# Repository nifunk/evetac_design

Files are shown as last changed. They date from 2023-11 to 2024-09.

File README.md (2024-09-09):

# evetac_design

<!-- PROJECT LOGO -->
<br />
<div align="center">
  <a href="https://github.com/nifunk/evetac_design">
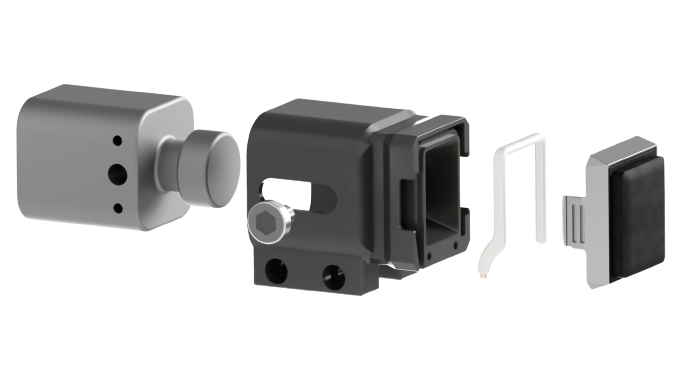
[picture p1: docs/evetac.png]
evetac_design
    
  </a>

  <h3 align="center">Evetac: An Event-based Optical Tactile Sensor
for Robotic Manipulation</h3>
  <h5 align="center">Niklas Funk, Erik Helmut, Georgia Chalvatzaki, Roberto Calandra, Jan Peters</h5>

  <p align="center">
    We introduce a new event-based optical tactile sensor called Evetac. Its modular design attempts to maximize the re-use of existing components to facilitate reproducibility. You can simply 3D print the housing and assemble the sensor yourself. This repo contains the mechanical design files of the sensor and additional adapters. They are designed to be 3D printed so that you are able to produce them yourself and/or modify them to fit your needs. <br />
    <a href="https://sites.google.com/view/evetac"><strong>For more information about Evetac, visit the Project Page. »</strong></a> <br />
    <a href="https://youtu.be/24e9n3mCopw"><strong>Click here for a Video Tutorial on how to assemble Evetac. »</strong></a>
  </p>
</div>

<!-- TABLE OF CONTENTS -->
<details>
  <summary>Table of Contents</summary>
  <ol>
    <li>
      <a href="#sensor-overview">Sensor Overview</a>
    </li>
    <li>
      <a href="#alternative-evetac-versions">Alternative Evetac Versions</a>
    </li>
    <li>
      <a href="#customization-and-3d-printing">Customization and 3D Printing</a>
    </li>
    <li>
      <a href="#questions-and-contributing">Questions and Contributing</a>
    </li>
    <li>
      <a href="#citing">Citing</a>
    </li>
  </ol>
</details>

<!-- Sensor Overview -->
## Sensor Overview
The sensor mainly consists of off-the-shelf components, as well as a 3D printed case for facilitating manufacturing and reducing the entry barrier into the field of event-based tactile sensing. You can find a detailed overview of the sensors components in the following table:

| Component | Specifications | References |
|---|---|---|
| Camera | DVXplorer Mini from Inivation, 640 x 480px resolution | <a href="https://shop.inivation.com">Inivation</a>  |
| Housing | Custom Design, 3D printed | <a href="/evetac_housing/evetac-housing.stl">Design File</a> |
| Camera Screws | 1/4", thread length 6.3mm | <a href="https://www.amazon.de/gp/product/B01AZ558WE/ref=ppx_yo_dt_b_asin_title_o01_s00?ie=UTF8&psc=1">Amazon</a> |
| LED stripe | LED COB band 4000K,  height 5mm, witdth 2.2mm, 12V  | <a href="https://www.amazon.de/gp/product/B09WHY4Q33/ref=ppx_yo_dt_b_asin_title_o00_s00?ie=UTF8&th=1">Amazon</a> |
| Gel | GelSight Mini Marker Gel | <a href="https://www.gelsight.com/product/tracking-marker-replacement-gel/">GelSight</a> |

All the adaptors for the Franka Emika Panda robot arm, Robotis RH-P12-RN gripper, and OptiTrack accessories that were used in the experiments can be found in the respective folders: <a href="/adapters">adapters</a> and <a href="/optitrack">optitrack</a>.

<!-- Alternative Evetac Versions -->
## Alternative Evetac Versions
To improve sensor reproducibility, we aim to provide additional Evetac Designs <a href="/evetac_housing/alternative_designs/">here</a>.
* December 2023: Adding support for the newly released DVXplorer Micro event-based camera from Inivation. 

<!-- Customization and 3D Printing -->
## Customization and 3D Printing
In case you want to customize the provided 3D models and print them on a 3D printer, you will need to download the .STEP files, modify them according to your needs and prepare it for the printer using specialized software. Here are the general steps to follow:

1. Choose a 3D modeling software: There are many 3D modeling software options available, both free and paid. Some popular options are <a href="https://www.autodesk.de/products/fusion-360">Fusion 360</a> or <a href="https://www.freecad.org/index.php?lang=de">FreeCAD</a>.
2. Customize the 3D model: Using the 3D modeling software, open the .STEP file of the object you want to edit and modify it to fit your needs. You can of course also create a new 3D model from scratch.
3. Export the file: Once the 3D model is complete, you will need to export it in a format that can be read by a 3D printer. The most common file format for 3D printing is .STL (STereoLithography).
4. Slice the file: The .STL file needs to be "sliced" into thin layers that the 3D printer can print one at a time. This is done using slicing software (e.g. <a href="https://ultimaker.com/de/software/ultimaker-cura">Cura</a> for <a href="https://de.wikipedia.org/wiki/Fused_Deposition_Modeling">FDM</a> 3D printers like the Prusa MK series), which takes the 3D model and creates a set of instructions that the 3D printer can understand.
5. Transfer the file: Once the file is sliced, it can be transferred to the 3D printer either through a SD Card, USB cable or wirelessly, depending on the printer.
6. Start printing: Load the 3D printer with the material you want to use (such as PLA or ABS), and start the printing process. The printer will then print the object layer by layer until it is complete.

Keep in mind that the specific steps for creating a 3D file may vary depending on the software and printer you are using. It is important to refer to the manufacturer's instructions and guides to ensure you are creating a file that is compatible with your 3D printer.

<!-- Questions and Contributing -->
## Questions and Contributing
If you have any questions or need help with setting up the sensor, please create an <a href="https://github.com/nifunk/evetac_design/issues/new">issue</a>.

We also welcome contributions to this repository, including new 3D models or other improvements. If you would like to contribute, please <a href="https://github.com/nifunk/evetac_design/fork">fork</a> this repository and submit a <a href="https://github.com/nifunk/evetac_design/compare">pull request</a> with your changes, or reach out to niklas [at] robot-learning [dot] de.

<!-- Citing -->
## Citing
If you use this project in your research, please cite it.

```
@ARTICLE{EvetacFunk,
  author={Funk, Niklas and Helmut, Erik and Chalvatzaki, Georgia and Calandra, Roberto and Peters, Jan},
  journal={IEEE Transactions on Robotics}, 
  title={Evetac: An Event-based Optical Tactile Sensor for Robotic Manipulation}, 
  year={2024},
  volume={},
  number={},
  pages={1-20},
  keywords={Robots;Tactile sensors;Optical sensors;Cameras;Robot vision systems;Optical feedback;Spatial resolution;Force and Tactile Sensing;Perception for Grasping and Manipulation;Deep Learning in Robotics and Automation;Event-based Sensing},
  doi={10.1109/TRO.2024.3428430}}
```

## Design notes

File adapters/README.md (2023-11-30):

# List of Adapters provided in this folder:

* <a href="/adapters/franka-robotis-interface.stl">franka-robotis-interface</a> - Interface part for attaching the Robotis Gripper to the end effector flange of the Franka Panda.
* <a href="/adapters/robotis-gripper-evetac-mount.stl">robotis-gripper-evetac-mount</a> - Part for attaching Evetac's mounting mechanism as a finger to the Robotis gripper. I.e., this part allows attaching Evetac's housing to the Robotis gripper.
* <a href="/adapters/gelsight-mini-evetac-mount.stl">gelsight-mini-evetac-mount</a> - Adapter for GelSight Mini such that it is compatible with Evetac's mounting mechanism.
* <a href="/adapters/robotis-gripper-gelsight-mini.stl">robotis-gripper-gelsight-mini</a> - Part for attaching GelSight Mini's mounting mechanism as a finger to the Robotis gripper. I.e., this part allows attaching GelSight Mini directly to the Robotis gripper.
* <a href="/adapters/franka-evetac-finger.stl">franka-evetac-finger</a> - Part for attaching Evetac as a single finger to the franka end effector mounting flange.
* <a href="/adapters/franka-gelsight-mini-finger.stl">franka-gelsight-mini-finger</a> - Part for attaching GelSight Mini as a single finger to the franka end effector mounting flange.
* <a href="/adapters/robotis-evetac-finger.stl">robotis-evetac-finger</a> - Part for attaching Evetac as a single finger to the franka-robotis-interface. Please note, this additionally requires inserting 4 threads into the holes on top using a soldering iron, such that the adapter can be connected to the robotis interface using screws.
* <a href="/adapters/robotis-gelsight-mini-finger.stl">robotis-gelsight-mini-finger</a> - Part for attaching GelSight Mini as a single finger to the franka-robotis-interface. Please note, this additionally requires inserting 4 threads into the holes on top using a soldering iron, such that the adapter can be connected to the robotis interface using screws.

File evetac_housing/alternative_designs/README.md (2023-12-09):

This folder provides additional Evetac Designs to improve reproducibility and recreate Evetac using different hardware components.

The table below lists the alternative sensor designs and which components deviate from the original design.

| Details | evetac_dvxplorer_micro  |
|---|---|
| Camera | DVXplorer Micro from Inivation, 640 x 480px resolution (from <a href="https://shop.inivation.com">Inivation</a>)  |
| Housing | Custom Design, 3D printed (<a href="/evetac_housing/alternative_designs/evetac_dvxplorer_micro/evetac_dvxplorer_micro-housing.stl">here</a>) |
| Camera Screws | 4 M2 Screws |
| LED stripe | Same as original Evetac |
| Gel | Same as original Evetac |

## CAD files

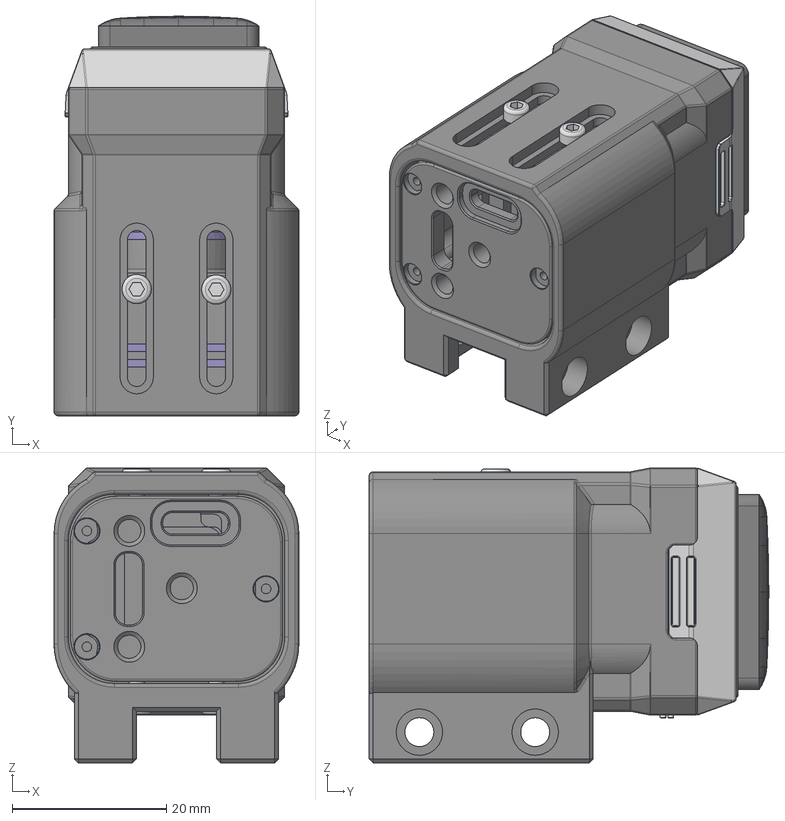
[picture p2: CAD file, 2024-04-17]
evetac_housing/alternative_designs/evetac_dvxplorer_micro/evetac_dvxplorer_micro-assembly.step
31.7 x 51.7 x 38.2 mm
evetac-housing
DVXplorer Micro 07.2023 Case v2
DVXplorer Micro 07.2023 Cover v2
evetac-gelsight-snapfitholder
Komponente2
Komponente3
Komponente2_1
screw x 4

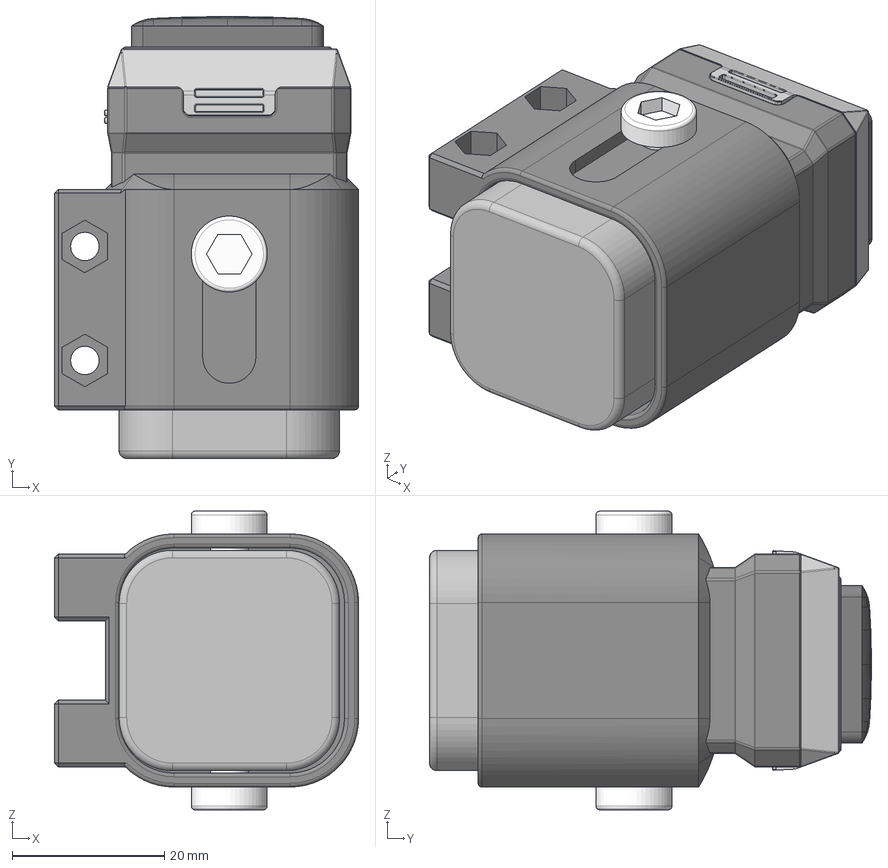
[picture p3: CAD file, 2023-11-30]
evetac_housing/evetac-assembly.step
40.0 x 58.1 x 39.3 mm
evetac-center
Komponente11
evetac-gelsight-snapfitholder
Komponente14
Komponente15
Komponente17
screw 1
screw 2

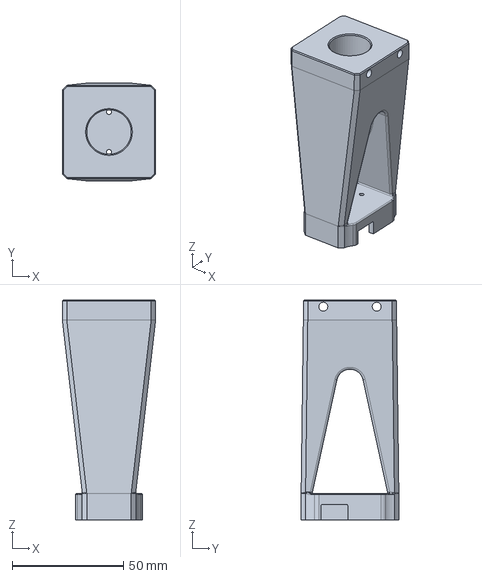
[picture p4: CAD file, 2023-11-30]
adapters/robotis-gelsight-mini-finger.step
42.0 x 44.0 x 99.0 mm
Komponente1
Komponente2

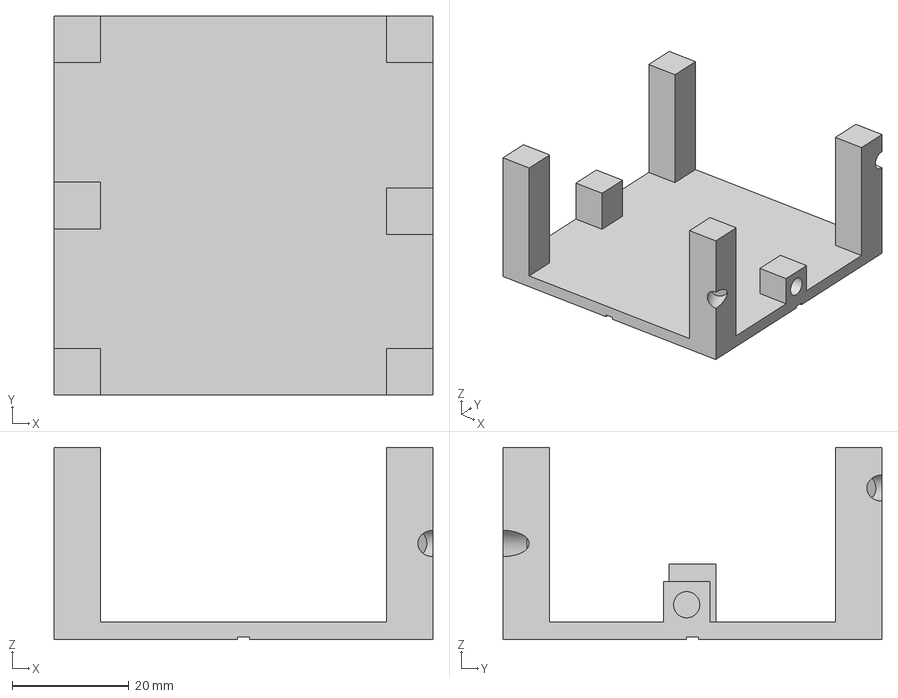
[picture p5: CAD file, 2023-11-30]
optitrack/evetac-optitrack-marker-holder-small.step
65.0 x 65.0 x 33.0 mm

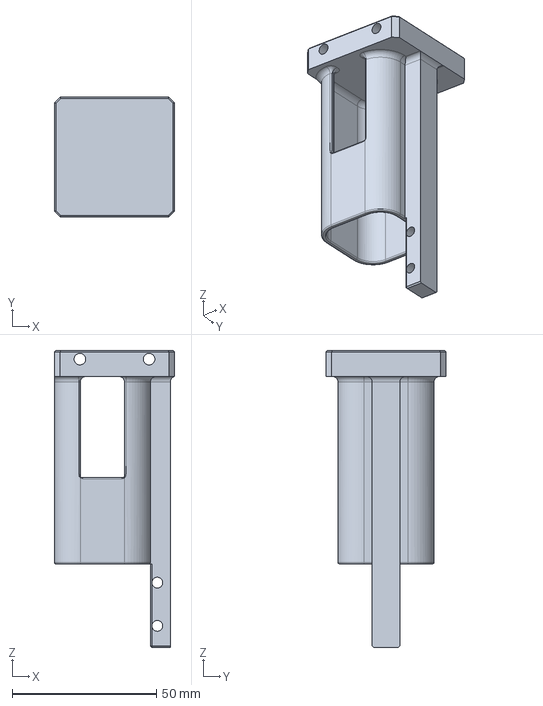
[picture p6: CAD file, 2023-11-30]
adapters/robotis-evetac-finger.step
41.7 x 41.7 x 103.0 mm

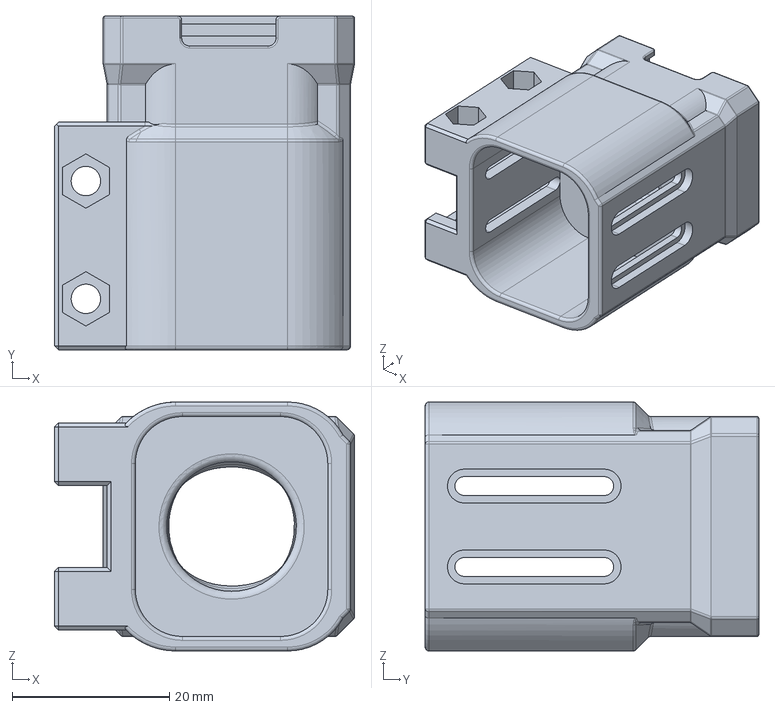
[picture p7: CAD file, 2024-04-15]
evetac_housing/alternative_designs/evetac_dvxplorer_micro/evetac_dvxplorer_micro-housing.step
38.2 x 42.5 x 31.7 mm

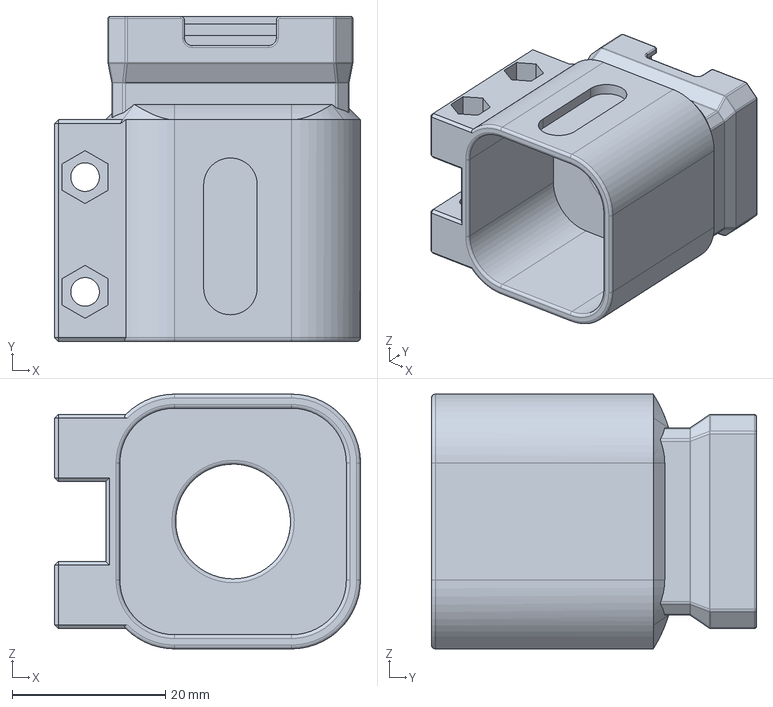
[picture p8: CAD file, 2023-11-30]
evetac_housing/evetac-housing.step
40.0 x 42.5 x 33.3 mm

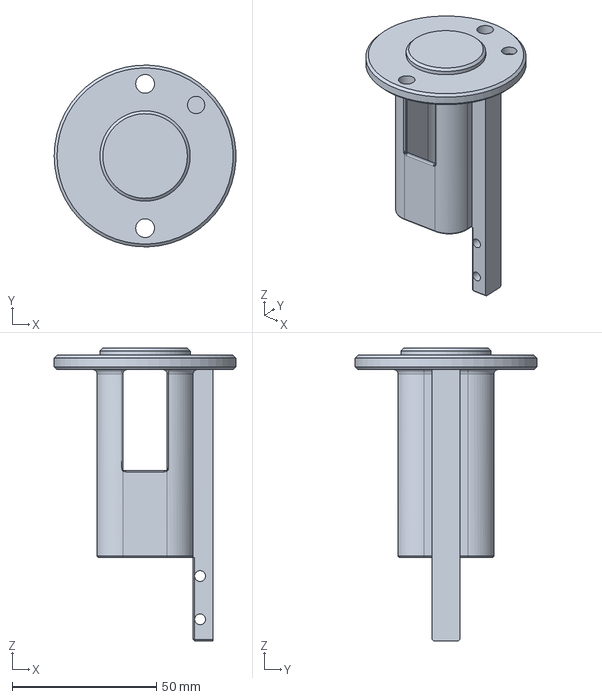
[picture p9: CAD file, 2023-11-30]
adapters/franka-evetac-finger.step
62.9 x 63.0 x 101.5 mm

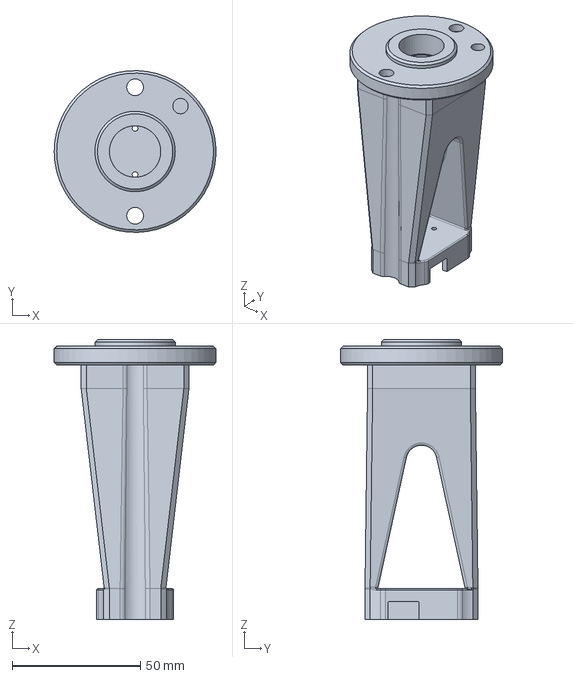
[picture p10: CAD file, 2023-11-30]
adapters/franka-gelsight-mini-finger.step
62.9 x 63.0 x 109.0 mm

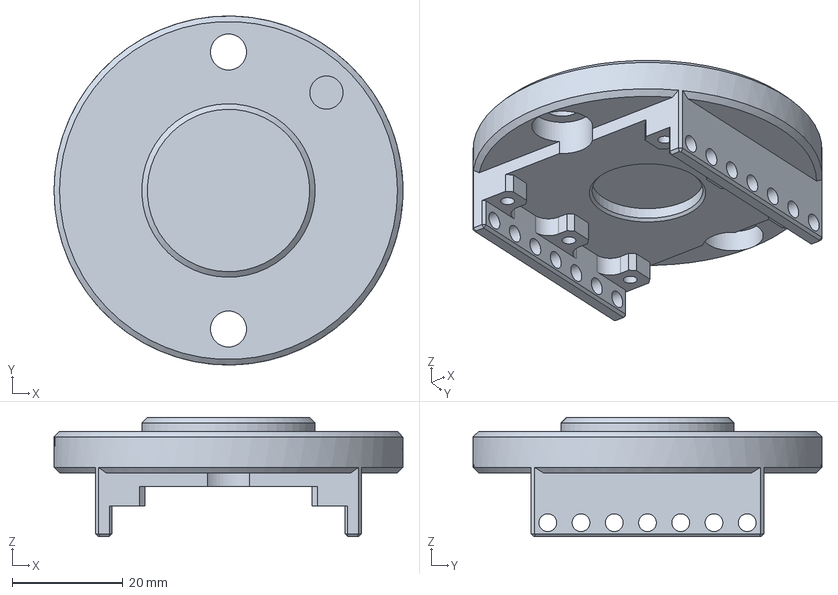
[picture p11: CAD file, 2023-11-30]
adapters/franka-robotis-interface.step
63.0 x 63.0 x 21.5 mm

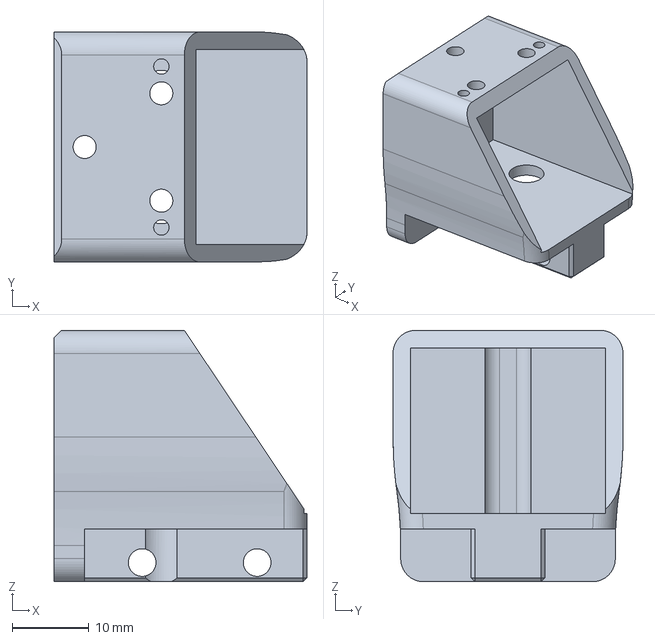
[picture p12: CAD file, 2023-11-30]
adapters/robotis-gripper-evetac-mount.step
33.0 x 30.0 x 32.8 mm

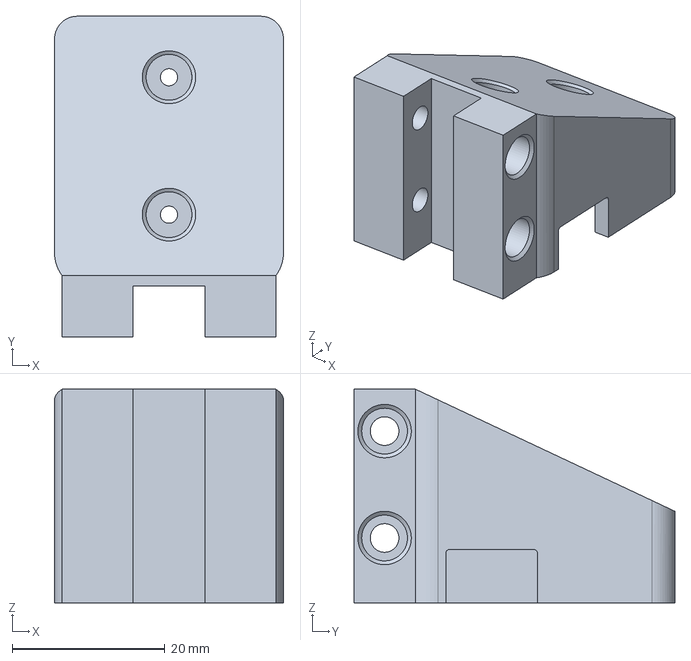
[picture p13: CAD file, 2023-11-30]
adapters/gelsight-mini-evetac-mount.step
30.0 x 42.0 x 28.0 mm

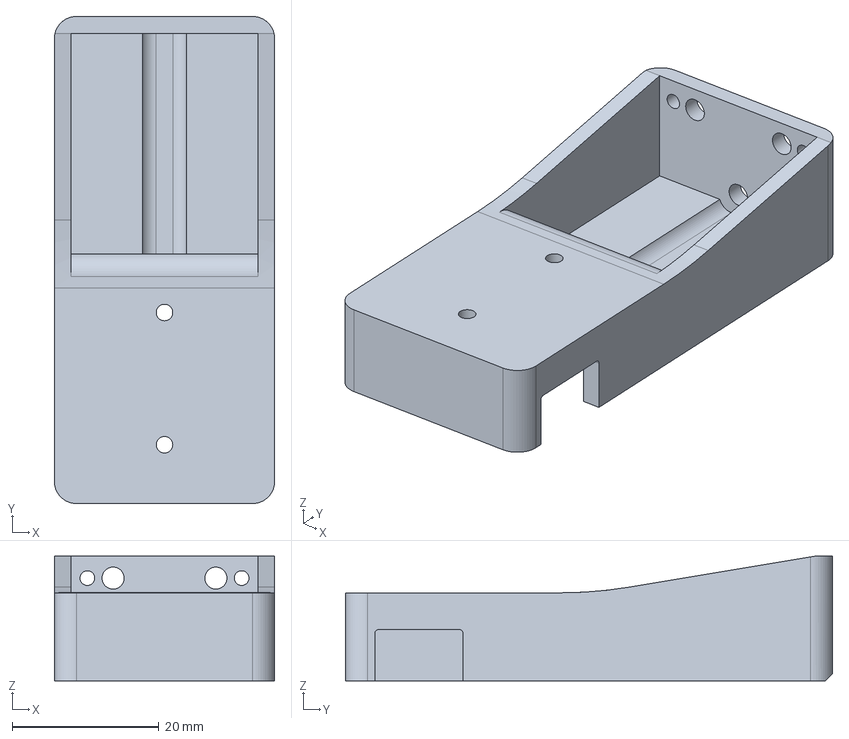
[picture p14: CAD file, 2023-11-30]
adapters/robotis-gripper-gelsight-mini.step
30.0 x 66.3 x 17.0 mm

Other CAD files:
adapters/franka-evetac-finger.stl
adapters/franka-gelsight-mini-finger.stl
adapters/franka-robotis-interface.stl
adapters/gelsight-mini-evetac-mount.stl
adapters/robotis-evetac-finger.stl
adapters/robotis-gelsight-mini-finger.stl
adapters/robotis-gripper-evetac-mount.stl
adapters/robotis-gripper-gelsight-mini.stl
evetac_housing/alternative_designs/evetac_dvxplorer_micro/evetac_dvxplorer_micro-housing.stl
evetac_housing/evetac-housing.stl
optitrack/evetac-optitrack-marker-holder-small.stl

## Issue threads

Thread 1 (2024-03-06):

robotis-gripper-gelsight-mini.stl

forestspike, 2024-03-06:
Thanks for your sharing.  Your works really help me a lot.

I have a question, in the adapters file, the **robotis-gripper-gelsight-mini.stl** is the part allows attaching GelSight Mini directly to the Robotis gripper. I wonder if it is suitable for **robotiq 85 gripper**?

nifunk, 2024-03-07:
Thanks for the message. Unfortunately I am not sure. Mainly, because I do not have access to a **robotiq 85 gripper** at the moment. If you have a robotiq 85 gripper, could you maybe send a picture of how the fingers are mounted / attached to the gripper? Alternatively a technical drawing would help. Then I can tell you for sure if it works or not.

nifunk, 2024-04-15:
Closing due to inactivity. Please feel free to reopen this issue if additional support is needed on this topic.

nifunk, 2024-04-15:
Closing due to inactivity. Please feel free to reopen this issue if additional support is needed on this topic.

Closed 2024-04-15.

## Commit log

2023-12-09 adding support for DVXplorer Micro
    [evetac_dvxplorer_micro-assembly.step, evetac_dvxplorer_micro-housing.step, evetac_dvxplorer_micro-housing.stl]
2024-04-15 Slight update on Evetacs housing - increasing wall thickness
    [evetac-housing.step, evetac-housing.stl]
2024-04-15 adding link to assembly video
2024-04-15 correcting mixup in 3D printing files
    [evetac-housing.step, evetac-housing.stl, evetac_dvxplorer_micro-housing.step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]
2024-04-17 adapting the housing in the assembly step file also
    [evetac_dvxplorer_micro-assembly.step]
